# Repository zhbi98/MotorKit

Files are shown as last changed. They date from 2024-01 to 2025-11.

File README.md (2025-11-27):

## ODriveX

一款基于 STM32F405 的高性能开源磁场定向控制（FOC）驱动器，逆变电路采用了英飞凌的 DirectFET-MOS 管，支持高达 100A 持续电流 和 3kW 电机功率，适用于机器人、无人机、CNC 等高动态应用场景。

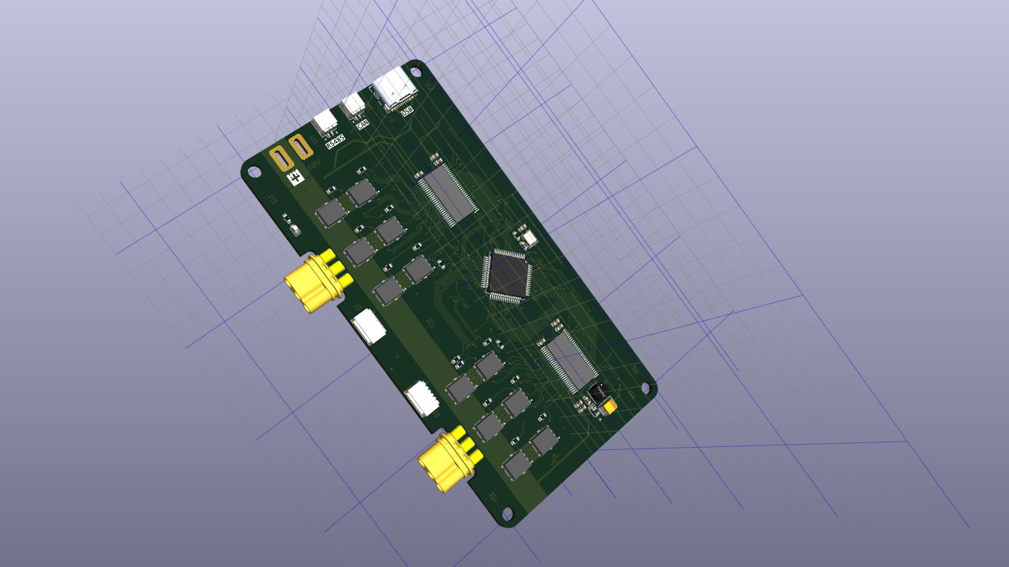
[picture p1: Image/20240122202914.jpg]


## 核心特性

(1) 高性能功率级：英飞凌 DirectFET MOSFET，60V 耐压，单路 100A 峰值电流

(2) 多总线通信：USB-CDC、UART、RS485（Modbus RTU）、CAN 2.0B

(3) 高精度反馈：支持 AS5047P（14-bit SPI）、ABI 编码器、UVW 霍尔

(4) 现代开发栈：CMake + ARM-GCC + VSCode + OpenOCD 图形化调试

(5) 完整 FOC 控制：电流/速度/位置三闭环，支持 SVPWM、死区补偿、弱磁控制

(6) Step/Dir 兼容：可对接传统运动控制器（如 GRBL、Marlin）

## 硬件

硬件涉及两部分，驱动器主体（驱动器硬件命名为 MotorKit）和编码器模块（AS5047P-Driver）。PCB 打样使用制造输出文件（Gerber），打样时把所有 Gerber 文件压缩为 .zip 文件提供给 PCB 制造商（例如嘉立创）即可，PCB 经过我打样验证无误，Gerber 文件在 HardWare/Gerber 目录下，可直接使用。

原理图和 PCB 使用开源 EDA 工具 KiCAD 设计的，如果你有 KiCAD 也知道怎么使用，可以自己去导出 Gerber 文件。

PCB 采用 4层板设计，如果要编辑 PCB 需要下载 KiCAD，还需要看些教程熟悉使用方法，当然这个 EDA 工具本身也非常易学。

购买电子元器件按照 HardWare 目录下的 ibom.html 表格购买。

KiCAD 官方下载链接： https://www.kicad.org/

驱动器主体 KiCAD 工程目录：HardWare/kiacd_project

编码器模块 KiCAD 工程目录：HardWare/AS5047P/HardWare/kiacd_project

制造输出文件（Gerber）目录：HardWare/Gerber

器件 BOM 目录：HardWare/ibom.html

## 固件

程序固件使用 CMake 进行构建的，然后用 ARM-GCC 进行编译的，并且可以搭配 VSCode 和 OpenOCD 进行图形化调试，当然你可以新建一个 STM32F405 的 Keil 工程，把程序组织到 Keil 中编译也可以。

使用 CMake 要求会编写 CMakeLists.txt 文件，不过我这里已经编写好了，在 Firmware 目录下可以看到。

PCB 上预留了 SWD 调试接口，固件固件就可以使用 SWD 下载。

如果没有 VSCode 的嵌入式开发环境，可以看看这篇文章：https://blog.csdn.net/jf_52001760/article/details/126826393

## 电机

我购买的无刷电机是大疆精灵 3 的拆机无刷电机 2312S 可以在淘宝搜索购买，电机到手后还要进行改装，在电机轴上安装供编码器检测的径向磁铁，磁铁尺寸为 6mmx2mm，磁铁安装注意同心度不要过度偏移，磁铁与编码器的间隙大概为 1.0mm。然后再把把 AS5047 编码器模块固定到电机尾部。

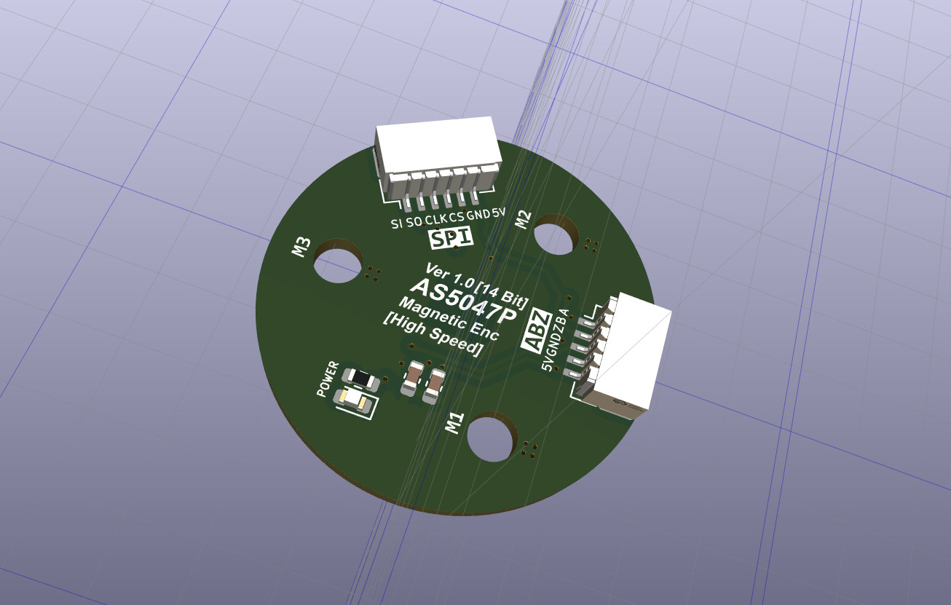
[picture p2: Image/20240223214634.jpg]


## Configuration

控制参数（例如 PID，电流，速度限制等等）都是包含默认值的，所以不需要逐个配置参数电机也能正常工作起来的，必须要注意的是根据实际编码器配置 cpr（例如 AS5047P 编码器使用 ABZ 接口时 CPR 为 1000x4=4000），index 参数，根据电机配置极对数 pole pairs（例如大疆 2312s 电机的极对数为 7），以及按实际调整电流采样电阻，配置一些必须变更的即可。

什么是极对数？

极数是指电机转子（即永磁体部分）磁场中磁极的总数量，磁极总数除以 2 就是极对数，极对数用 P 表示，每个极对包含一个北磁极 N 和一个南磁极 S。

## Start-up

(1) 电机校准（实际就是测量电机的相电阻和相电感）。

(2) 搜索定位编码器 index 信号（在编码器偏移校准之前必须先搜索 index）。

(3) 编码器偏移校准（Offset 校准）。

(4) 使能闭环状态/开环状态。

(5) 设置控制模式（控制模式包含：位置模式，速度模式，电流模式）。和 (4) 结合起来就得到，位置闭环控制模式，速度闭环控制模式，电流闭环控制模式。

(6) 设置控制模式目标值（位置值，速度值，电流值）来调节电机运行状态。

(7) 电机因异常停止后清除错误重新使能进入闭环状态即可。

## Command

CAN 通信协议和 Shell 交互命令实现分别位于 [communication/can/odrive_can.cpp](communication/can/odrive_can.cpp) 和 [ThirdParty/LetterShell/src/shell_cmd_list.c](ThirdParty/LetterShell/src/shell_cmd_list.c) 文件，具体可查看这两个文件，这里列出电机运行起来必要的 Shell 指令，使用 USB 数据线线连接板子 TypeC 和 PC，在 PC 上使用串口调试助手
下发下列指令即可控制。

```cpp
设置最大负电流
odrive:/$ dc_max_negative_current "-2.0"

速度限制 50 turn/s
odrive:/$ controller_config_vel_limit 0 "50.0"

设置电机 0 进入校准状态
odrive:/$ axis_requested_state 0 3

设置电机 0 进入力矩控制模式
odrive:/$ controller_config_control_mode 0 1

设置电机 0 控制力矩
odrive:/$ controller_input_torque 0 "0.02"

进入闭环
odrive:/$ axis_requested_state 0 8

打印当前错误
odrive:/$ dump_errors 1
```

## Step/Dir

Choose any two of the unused GPIOs for step/dir input. Let’s say you chose GPIO7 for the step signal and GPIO8 for the dir signal.

选择任意两个未使用的 GPIO 即可用于 step 和 dir 信号步骤/输入，假设您选择 GPIO7 作为步长信号，GPIO8 选择用于 dir 信号。

这种是基于 step 对应 GPIO 中断对外部电平输入步数累计（中断次数累计），达到位置控制信号可以通过普通 GPIO 输入的目的，

注意这不是 PWM 输入控制模式，两者是有区别的。

This is the simplest possible way of controlling the ODrive. It is also the most primitive and fragile one. So don’t use it unless you must interoperate with other hardware that you don’t control.

这是给驱动器提供控制指令信号最简单的方法。 它也是最原始且最脆弱的一个。因此,除非必须与其他无法控制的硬件进行互操作,否则请勿使用。

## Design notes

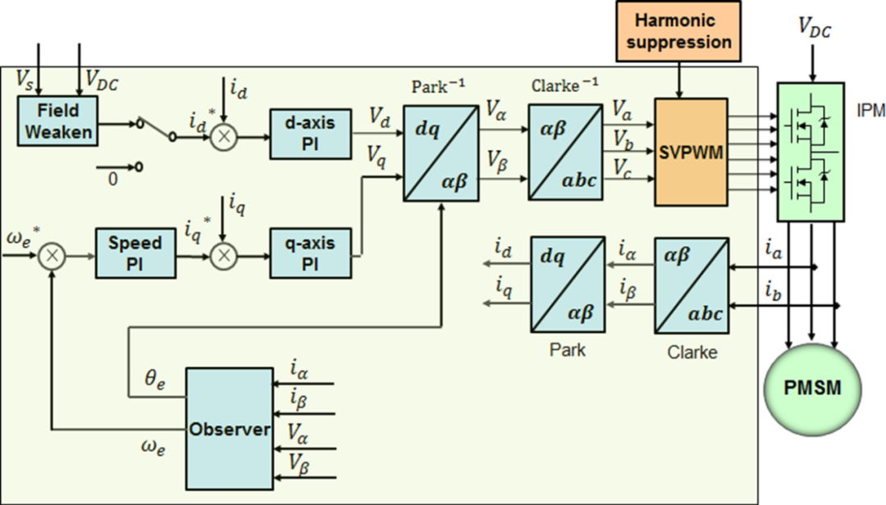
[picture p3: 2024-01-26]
Docs/Control/FOC控制系统框图.png

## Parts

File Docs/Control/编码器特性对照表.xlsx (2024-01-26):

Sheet: Rotary
 | Type | Resolution | Noise (RMS) | max speed | Price | link | Interfaces |  |  | Electrical connection |  | Notes
Note: only encoders with bandwidth (filter cutoff) >200Hz are considered |  | Count/rev | deg | RPM | for 10 units |  | Quadrature | index | absolute | Single ended | Differential
Generic 600ppr encoder | shaft | 2400 | 0.0433 | 4500 | 12 | https://www.aliexpress.com/item/360-600P-R-Photoelectric-Incremental-Rotary-Encoder-5-24V-AB-Two-Phases-Shaft/32756209569.html | y | n | n | y | n
CUI - AMT102 | through bore | 8192 | 0.0127 | 7500 | 24 | https://www.digikey.com/product-detail/en/cui-inc/AMT102-V/102-1307-ND/827015 | y | y | n | y | y
CUI - AMT112 | through bore | 16384 | 0.0063 | 4000 | 32 | https://www.digikey.com/product-detail/en/cui-inc/AMT112S-V/102-3316-ND/4835227 | y | y | n | y | y
USDigital - E6 | through bore | 40000 | 0.0026 | 4320 | 67 | https://www.usdigital.com/products/encoders/incremental/rotary/kit/E6 | y | y | n | y | y
CUI - AMT232B | through bore | 16384 | 0.0063 | 4000 | 49 | https://www.digikey.com/product-detail/en/cui-inc/AMT232B-V/102-4485-ND/8031587 | n | y | y | y | n
CUI - AMT212B | through bore | 16384 | 0.0063 | 4000 | 49 | https://www.digikey.com/product-detail/en/cui-inc/AMT212B-V/102-4527-ND/8537386 | n | y | y | n | y
AMS - AS5047P | on-axis chip | 16384 | 0.0680 | 28000 | 10.61 | https://www.digikey.com/product-detail/en/ams/AS5047P-ATSM/AS5047P-ATSMCT-ND/5287312 | n | y | y | y | n
AMS - AS5047U | on-axis chip | 16384 | 0.0480 | 28000 |  |  | y | y | y | y | n | NPI, not yet stocked?
MagAlpha - MA702 | on-axis chip | 4096 | 0.0300 | 60000 | 5.1 | https://www.digikey.com/product-detail/en/monolithic-power-systems-inc/MA702GQ-Z/1589-1516-1-ND/9433282 | n | y | y | y | n
Infineon - TLE5012 | on-axis chip | 16384 | 0.0500
AMS - AS5311 (w 128p mag ring) | multipole off-axis | 262144 | 0.0017 | 1099.21875 | 15 | https://www.digikey.com/product-detail/en/ams/AS5311-ATST-500/AS5311-ATST-500CT-ND/5892379 | y | n | n | y | n | Has stocking issues
Firmware to read absolute encoders coming soon.
ODrive does not have a receiver for differential encoders, you will have to add that yourself.

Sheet: Linear
 | Type | Resolution | Noise (RMS) | max speed | Price | link | Interfaces |  |  | Electrical connection |  | Notes
Note: only encoders with bandwidth (filter cutoff) >200Hz are considered |  | um | um | m/s | for 10 units |  | Quadrature | index | absolute | Single ended | Differential
AMS - AS5311 | magnetic | 0.49 | 0.60 | 2.35 | 12 | https://www.digikey.com/product-detail/en/ams/AS5311-ATST-500/AS5311-ATST-500CT-ND/5892379 | y | y | y | y | n | Has stocking issues
USDigital - EM2 | transmissive | 3.18 | 0.92 | 9.10 | 35 | https://www.usdigital.com/products/encoders/incremental/modules/EM2 | y | y | n | y | n

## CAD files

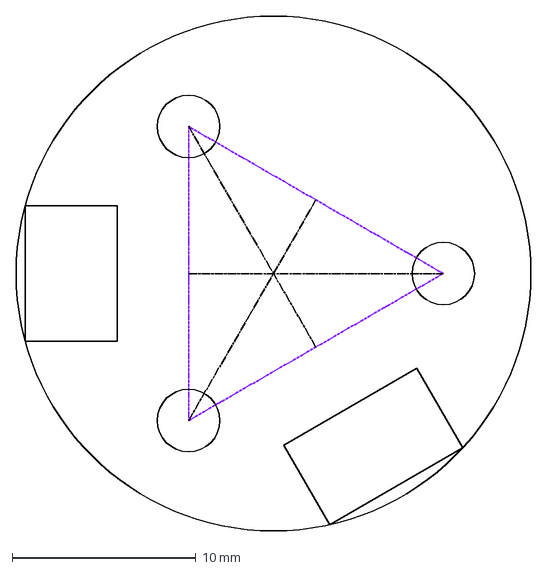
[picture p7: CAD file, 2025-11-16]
HardWare/AS5047P/AS5047P_TOP.dxf
28.0 x 28.0 mm

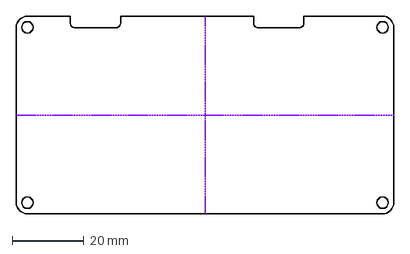
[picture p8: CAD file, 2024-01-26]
HardWare/EDG.dxf
105.0 x 55.0 mm

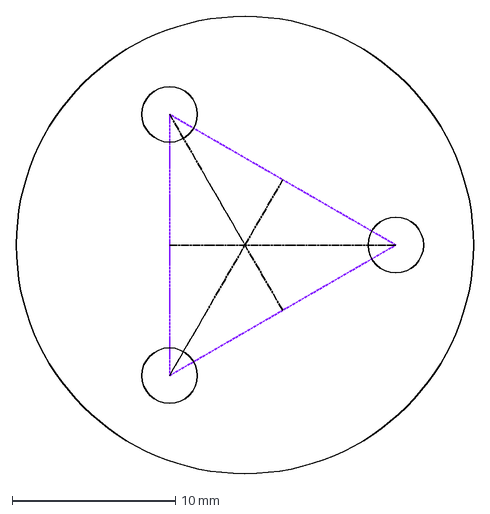
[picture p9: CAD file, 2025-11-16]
HardWare/AS5047P/AS5047P_EDG.dxf
28.0 x 28.0 mm

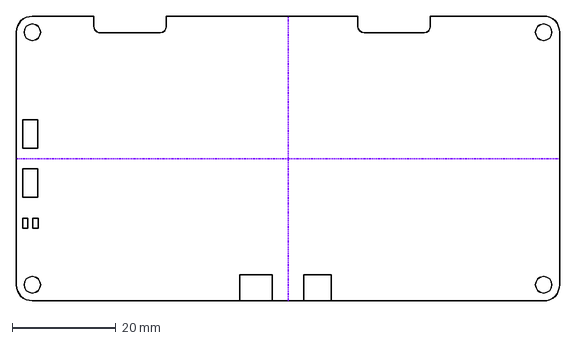
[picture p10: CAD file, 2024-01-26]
HardWare/BOM.dxf
105.0 x 55.0 mm

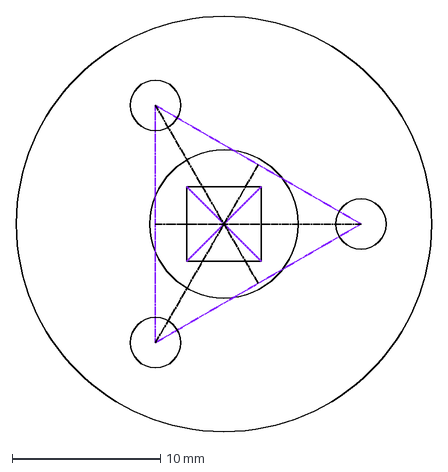
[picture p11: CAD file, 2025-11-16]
HardWare/AS5047P/AS5047P_BOM.dxf
28.0 x 28.0 mm

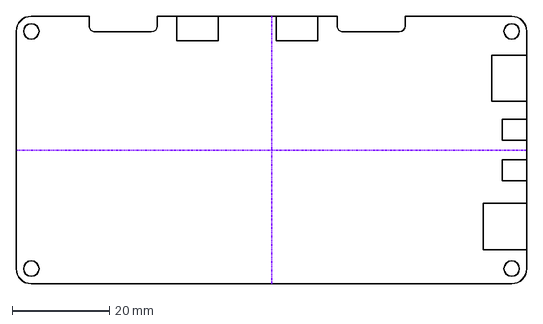
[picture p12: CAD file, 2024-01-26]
HardWare/TOP.dxf
105.0 x 55.0 mm

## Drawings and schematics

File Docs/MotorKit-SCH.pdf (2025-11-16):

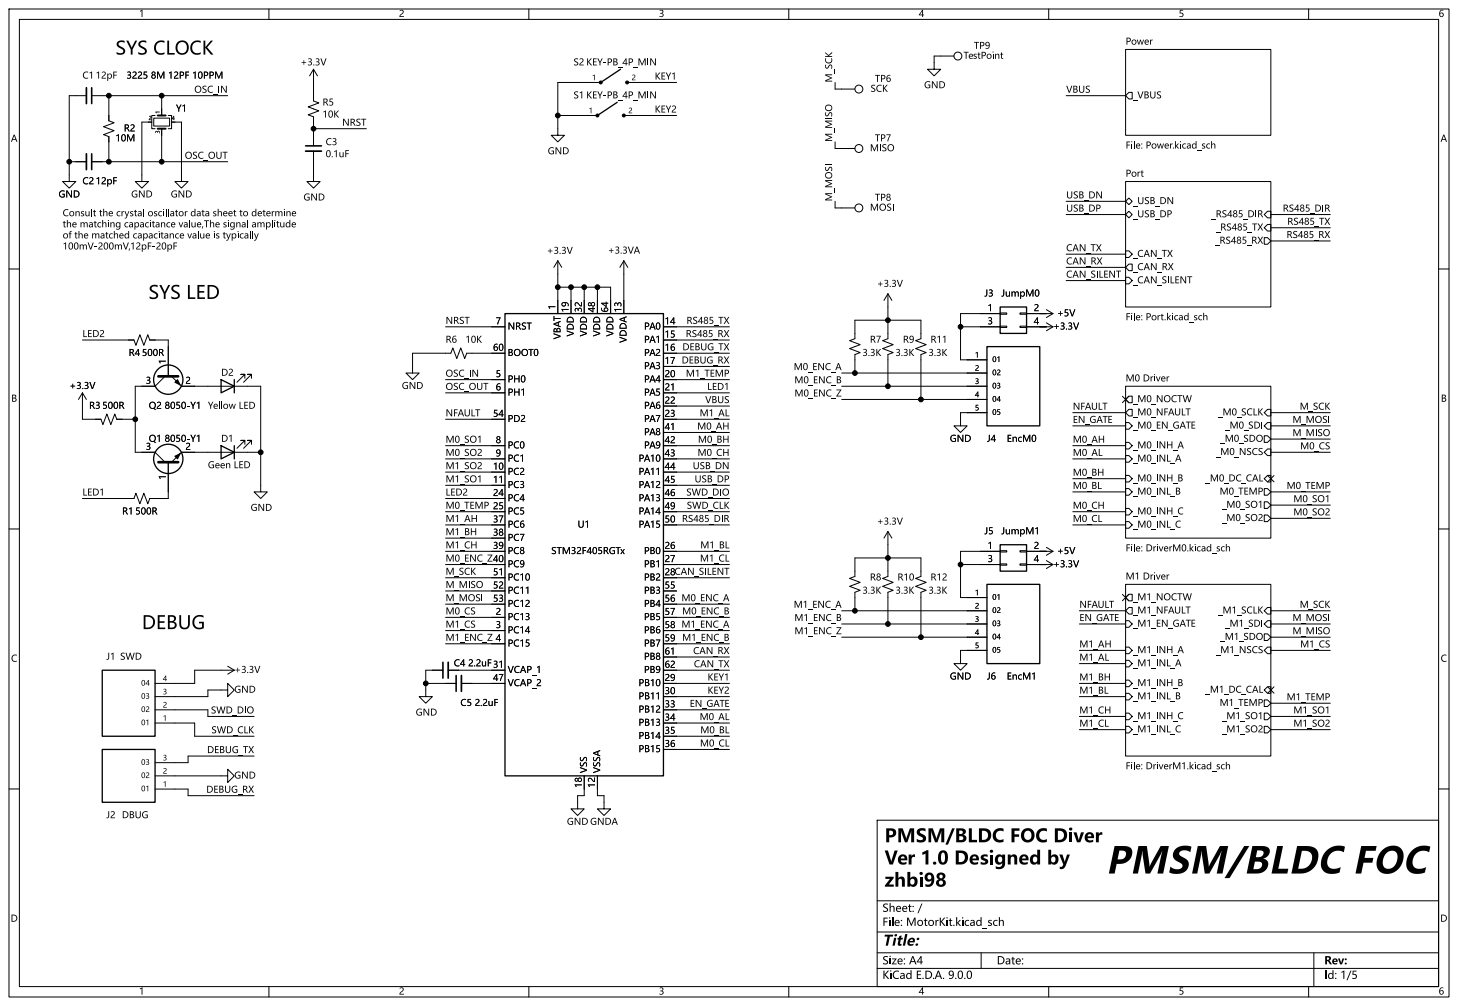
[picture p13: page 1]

GND
of the matched capacitance value is typically

1 VDD 19 VDD 32 VSS 18 VDD 48 VSSA 12 VDD 64 VDDA 13 PA0

Id: 1/5 Title: File: MotorKit.kicad_sch Sheet: /

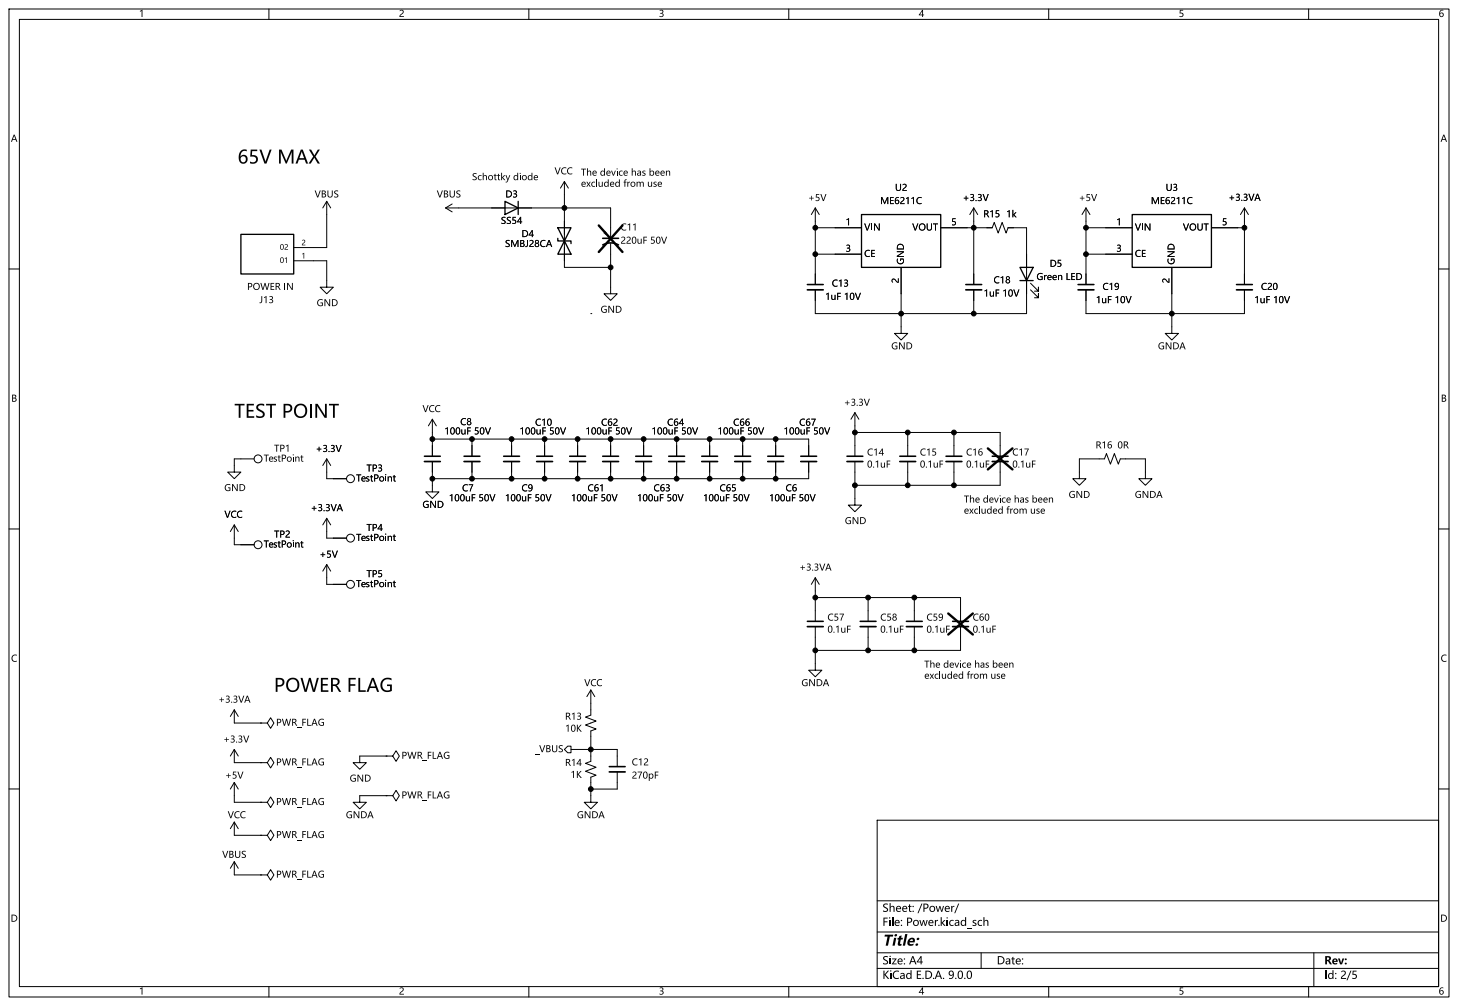
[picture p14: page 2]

The device has been
VCC

excluded from use TESTPOINT

Id: 2/5 Title: File: Power.kicad_sch Sheet: /Power/ C65

excluded from use POWER FLAG

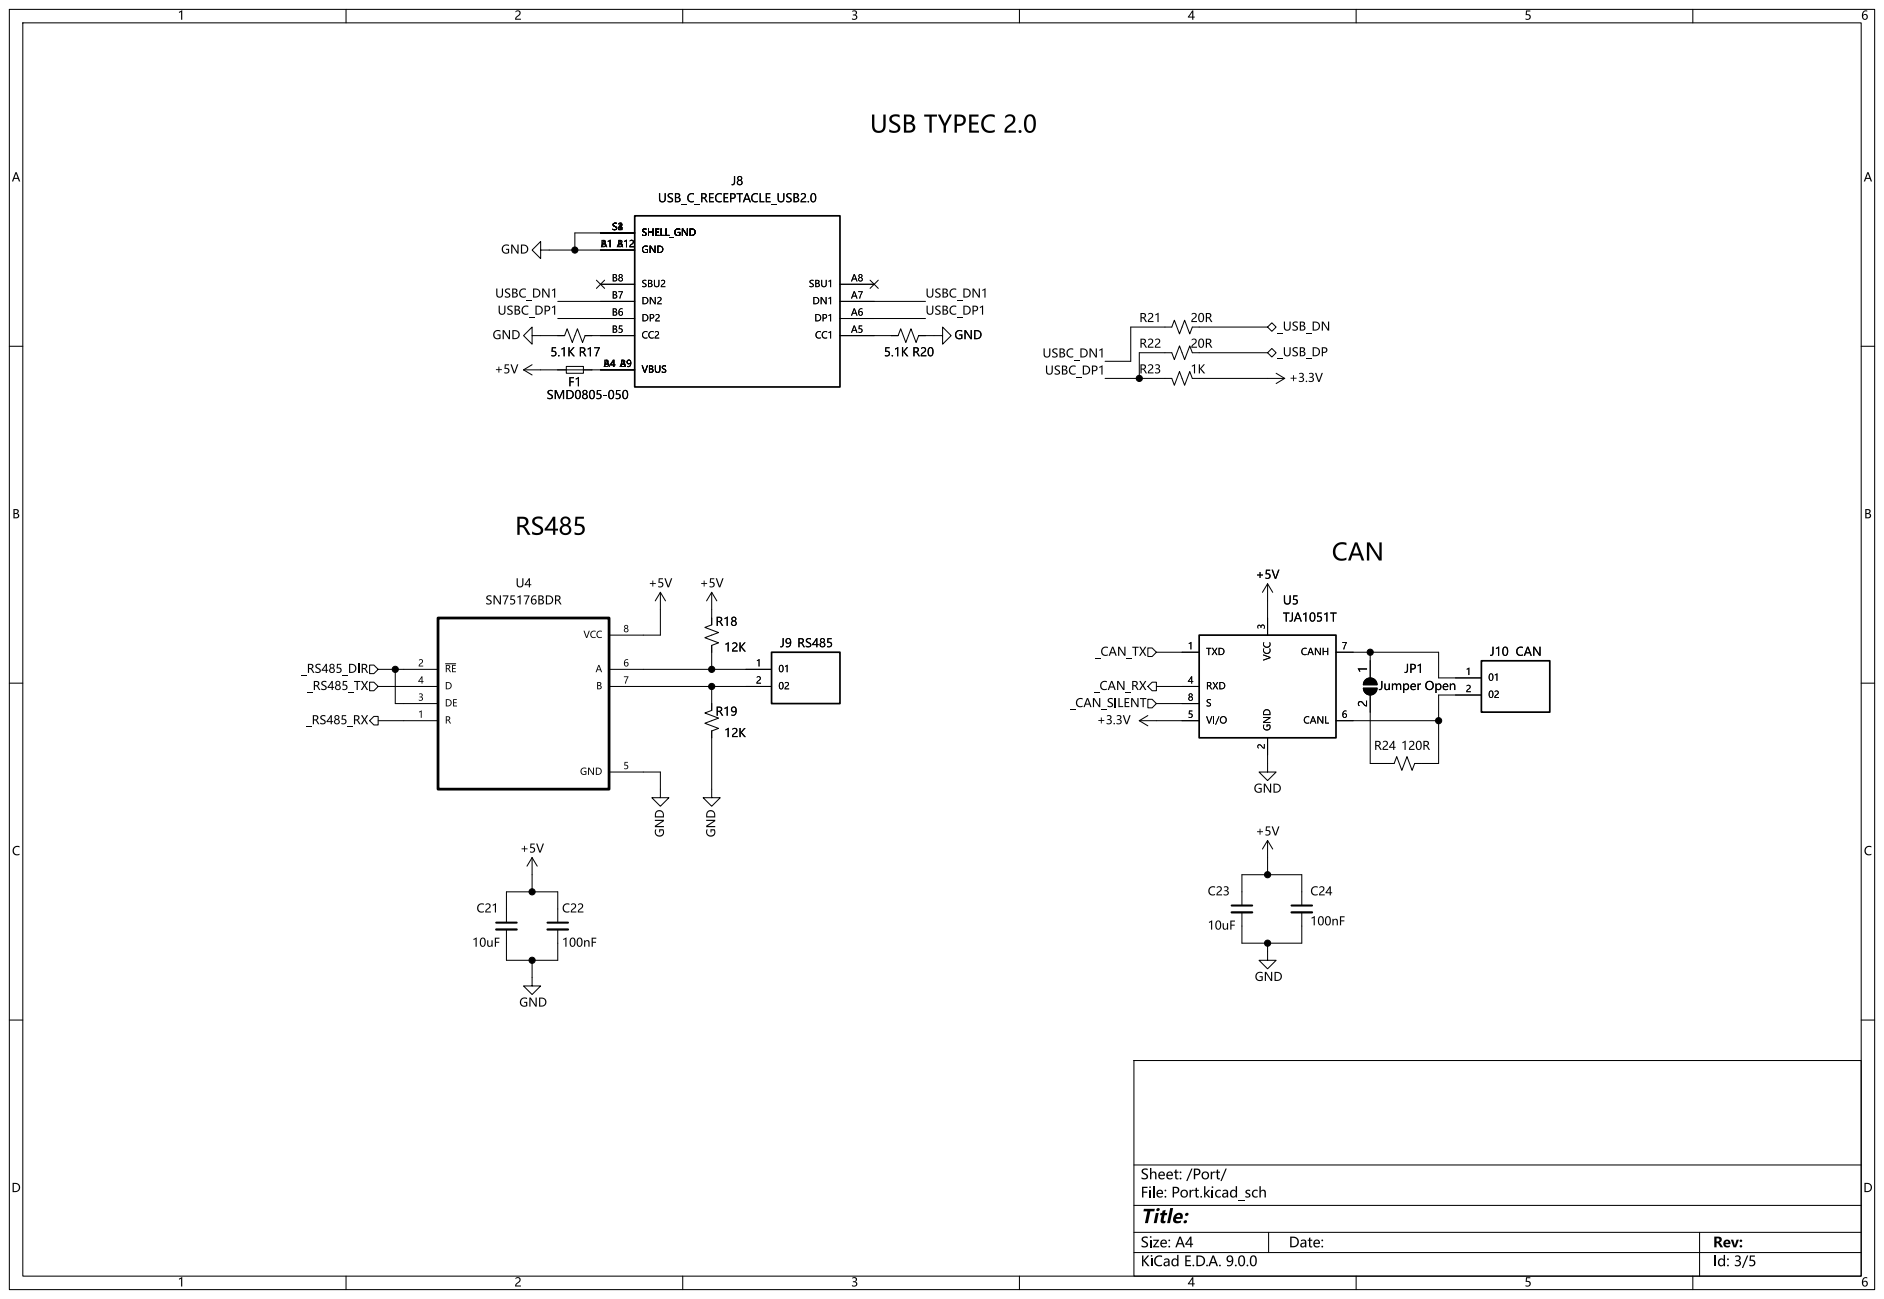
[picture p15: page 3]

Id: 3/5 Title: File: Port.kicad_sch Sheet: /Port/

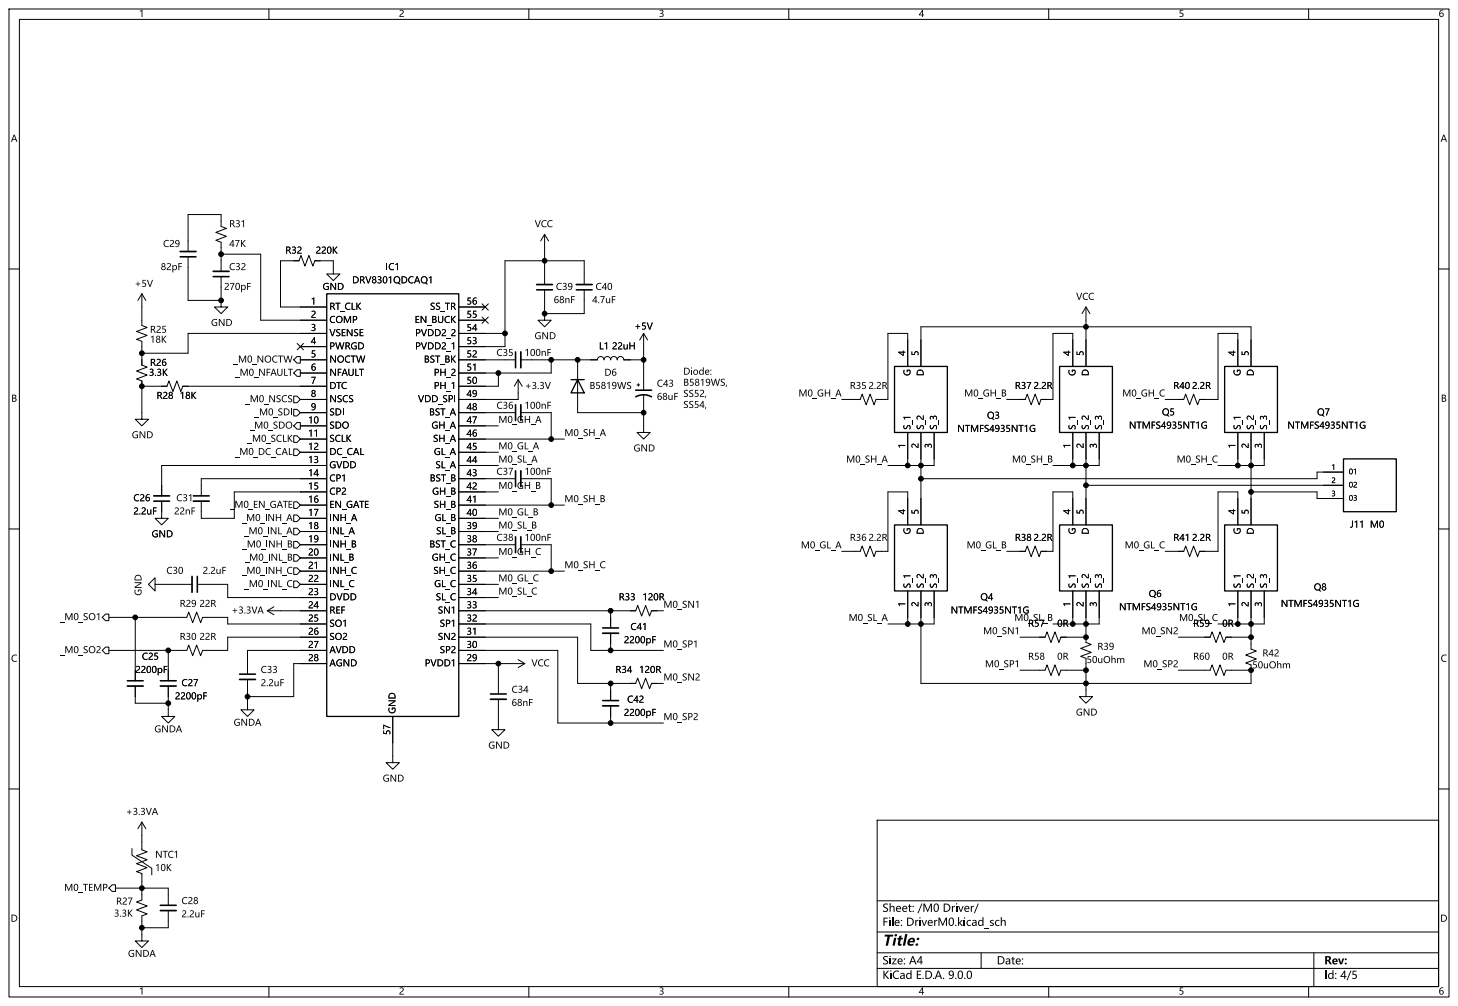
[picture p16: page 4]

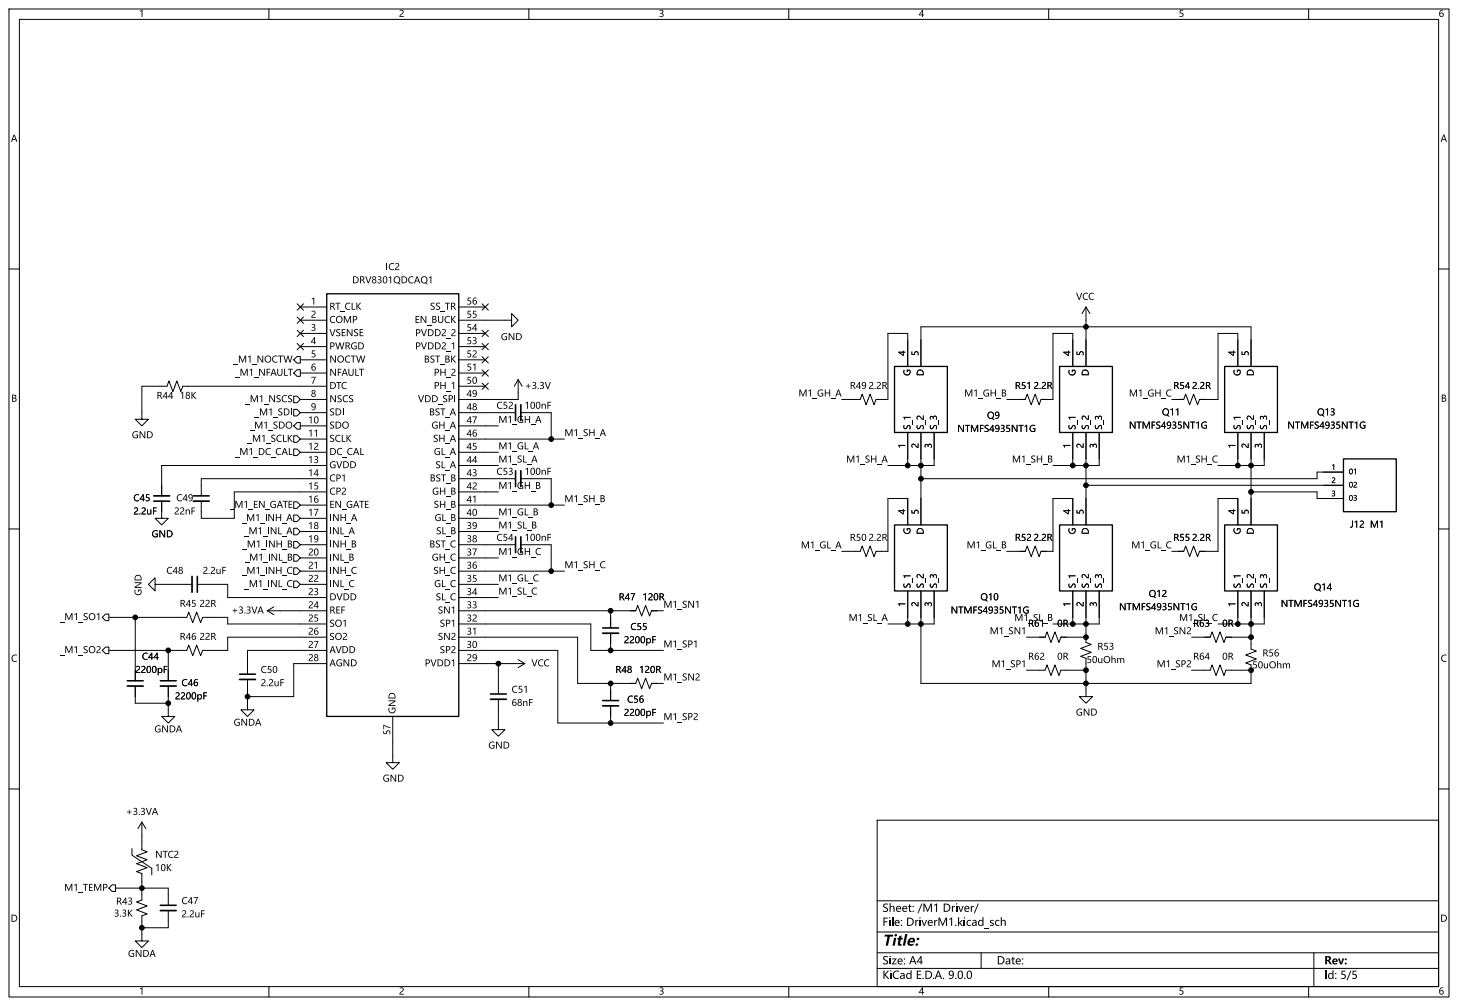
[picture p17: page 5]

Id: 5/5 Title: File: DriverM1.kicad_sch Sheet: /M1 Driver/

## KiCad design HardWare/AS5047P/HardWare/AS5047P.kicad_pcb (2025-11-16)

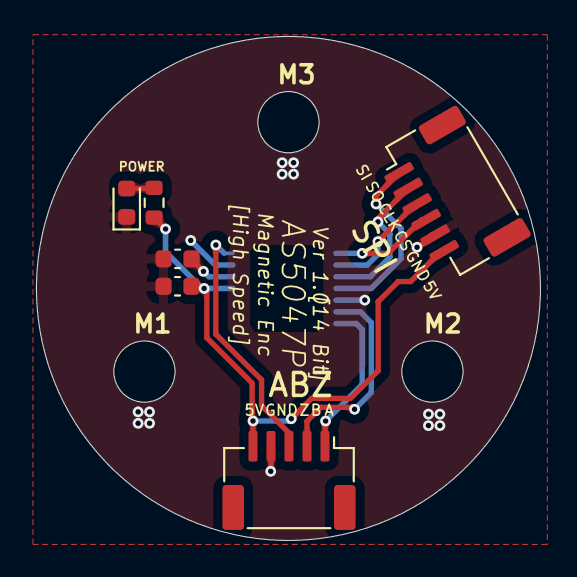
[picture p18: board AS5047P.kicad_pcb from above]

Board: 2 copper layers, 28.0 x 28.0 mm, 7 parts (1 on the bottom side), 11 nets.

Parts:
C1: 0.1uF; C_0603_1608Metric
C2: 1uF; C_0603_1608Metric
D1: Yellow LED; LED_0603_1608Metric
J1: CONN_1x5P; CONN-SMD_1x5P-P1.0-H_WAFER-SH1.0-5PWB
J2: CONN_1x5P; CONN-SMD_1x6P-P1.0-H_WAFER-SH1.0-6PWB
R1: 1K; R_0603_1608Metric
U1: AS5047D; TSSOP-14_4.4x5mm_P0.65mm

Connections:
+5V: C1.2, J1.5, J2.6, R1.1, U1.11 (VDD)
/A: J1.1, U1.7 (A)
/B: J1.2, U1.6 (B)
/CLK: J2.3, U1.2 (CLK)
/CS: J2.4, U1.1 (~CS)
/MISO: J2.2, U1.3 (MISO)
/MOSI: J2.1, U1.4 (MOSI)
/Z: J1.3, U1.14 (I/PWM)
GND: C1.1, C2.2, D1.1 (K), J1.4, J2.5, U1.5 (TST), U1.13 (GND)
unnamed: D1.2 (A), R1.2
unnamed: C2.1, U1.12 (VDD3V3)

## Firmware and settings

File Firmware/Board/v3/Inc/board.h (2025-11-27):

/*
* @brief Contains board specific configuration for ODrive v3.x
*/

#ifndef __BOARD_CONFIG_H
#define __BOARD_CONFIG_H

#include <stdbool.h>

// STM specific includes
#include <stm32f4xx_hal.h>
#include <gpio.h>
#include <spi.h>
#include <tim.h>
#include <can.h>
#include <i2c.h>
#include <usb_device.h>
#include <main.h>
#include "cmsis_os.h"

#include <arm_math.h>

#include <Drivers/STM32/stm32_system.h>

/*------ Add by zhbi98 -------*/
#define HW_VERSION_VOLTAGE 56U
#define HW_VERSION_MAJOR 3U
#define HW_VERSION_MINOR 6U
/*----------------------------*/

/*------ Modify by zhbi98 ----*/
/*相电流采样电阻设置，该定义要与实际电阻相同或接近，但相差不要超过 10 倍，例如实际为 5mΩ 可以设置为 2mΩ，
但不能设置为 0.5mΩ，否则可能会导致采集不到正确的电流从而产生 ERROR_PHASE_RESISTANCE_OUT_OF_RANGE 和 
ERROR_PHASE_INDUCTANCE_OUT_OF_RANGE 错误。*/
#define SHUNT_RESISTANCE (200e-5f/*500e-6f*/)
/*----------------------------*/

#define AXIS_COUNT (2)
#define CAN_CLK_MHZ (42UL)
#define CAN_CLK_HZ (42000000UL)
#define CAN_FREQ (2000000UL) /*42M/(16tq+4tq+1)*/

#define DEFAULT_BRAKE_RESISTANCE (2.0f) // [ohm]
#define DEFAULT_MIN_DC_VOLTAGE 8.0f

#define TIM_TIME_BASE TIM14

// Run control loop at the same frequency as the current measurements.
#define CONTROL_TIMER_PERIOD_TICKS  (2 * TIM_1_8_PERIOD_CLOCKS * (TIM_1_8_RCR + 1))

#define TIM1_INIT_COUNT (TIM_1_8_PERIOD_CLOCKS / 2 - 1 * 128) // TODO: explain why this offset

// The delta from the control loop timestamp to the current sense timestamp is
// exactly 0 for M0 and TIM1_INIT_COUNT for M1.
#define MAX_CONTROL_LOOP_UPDATE_TO_CURRENT_UPDATE_DELTA (TIM_1_8_PERIOD_CLOCKS / 2 + 1 * 128)

#ifdef __cplusplus
#include <Drivers/DRV8301/drv8301.hpp>
#include <Drivers/STM32/stm32_gpio.hpp>
#include <Drivers/STM32/stm32_spi_arbiter.hpp>
#include <MotorControl/pwm_input.hpp>
#include <MotorControl/thermistor.hpp>

using TGateDriver = Drv8301;
using TOpAmp = Drv8301;

#include <MotorControl/motor.hpp>
#include <MotorControl/encoder.hpp>

extern std::array<Axis, AXIS_COUNT> axes;
extern Motor motors[AXIS_COUNT];
extern OnboardThermistorCurrentLimiter fet_thermistors[AXIS_COUNT];
extern Encoder encoders[AXIS_COUNT];

extern USBD_HandleTypeDef& usb_dev_handle;

extern PwmInput pwm0_input;
#endif

// Period in [s]
#define CURRENT_MEAS_PERIOD ( (float)2*TIM_1_8_PERIOD_CLOCKS*(TIM_1_8_RCR+1) / (float)TIM_1_8_CLOCK_HZ )
static const float current_meas_period = CURRENT_MEAS_PERIOD;

// Frequency in [Hz]
#define CURRENT_MEAS_HZ ( (float)(TIM_1_8_CLOCK_HZ) / (float)(2*TIM_1_8_PERIOD_CLOCKS*(TIM_1_8_RCR+1)) )
static const int current_meas_hz = CURRENT_MEAS_HZ;

#if HW_VERSION_VOLTAGE >= 48
#define VBUS_S_DIVIDER_RATIO 19.0f
#elif HW_VERSION_VOLTAGE == 24
#define VBUS_S_DIVIDER_RATIO 11.0f
#else
#error "unknown board voltage"
#endif

// Linear range of the DRV8301 opamp output: 0.3V...5.7V. We set the upper limit
// to 3.0V so that it's symmetric around the center point of 1.65V.
#define CURRENT_SENSE_MIN_VOLT  0.3f
#define CURRENT_SENSE_MAX_VOLT  3.0f

// This board has no board-specific user configurations
static inline bool board_read_config() { return true; }
static inline bool board_write_config() { return true; }
static inline void board_clear_config() { }
static inline bool board_apply_config() { return true; }

void system_init();
bool board_init();
void start_timers();

#endif // __BOARD_CONFIG_H

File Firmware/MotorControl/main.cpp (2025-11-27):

#define __MAIN_CPP__
#include "odrive_main.h"
#include "nvm_config.hpp"

#include "usart.h"
#include "freertos_vars.h"
#include "usb_device.h"

osSemaphoreId sem_usb_irq;
osMessageQId uart_event_queue;
osMessageQId usb_event_queue;
osSemaphoreId sem_can;

#if defined(STM32F405xx)
// Place FreeRTOS heap in core coupled memory for better performance
__attribute__((section(".ccmram")))
#endif
uint8_t ucHeap[configTOTAL_HEAP_SIZE];
// FreeRTOS 允许应用程序开发者在外部定义堆的数组，同时利用 ".ccmram" 指令，将
// FreeRTOS 的堆数组放在 STM32 的 ccm 内存（CCM-RAM）中可以获得更好的性能。

uint32_t _reboot_cookie __attribute__ ((section (".noinit")));
extern char _estack; // provided by the linker script


ODrive odrv{};


ConfigManager config_manager;

static bool config_read_all() {
    /**从 NVM (芯片 Flash) 中加载 (读取) '板载配置参数' config_ 字段，
    编码器偏移校准参数到指定的各个结构体对象指针（内存）中。*/
    bool success = board_read_config() &&
           config_manager.read(&odrv.config_) &&
           config_manager.read(&odrv.can_.config_);

    /**从 NVM (芯片 Flash) 中加载 (读取) '电机配置参数'，config_ 字段，
    编码器偏移校准参数到指定的各个结构体对象指针（内存）中。*/
    for (size_t i = 0; (i < AXIS_COUNT) && success; ++i) {
        success = config_manager.read(&encoders[i].config_) &&
                  config_manager.read(&axes[i].sensorless_estimator_.config_) &&
                  config_manager.read(&axes[i].controller_.config_) &&
                  config_manager.read(&axes[i].trap_traj_.config_) &&
                  config_manager.read(&axes[i].min_endstop_.config_) &&
                  config_manager.read(&axes[i].max_endstop_.config_) &&
                  config_manager.read(&axes[i].mechanical_brake_.config_) &&
                  config_manager.read(&motors[i].config_) &&
                  config_manager.read(&motors[i].fet_thermistor_.config_) &&
                  config_manager.read(&motors[i].motor_thermistor_.config_) &&
                  config_manager.read(&axes[i].config_);
    }
    return success;
}

static bool config_write_all() {
    /**板载配置参数没有集中定义，而是分布定义到各个对象的 config_ 字段，
     * 各个对象的config_ 字段写入 NVM (芯片 Flash) 中。*/
    bool success = board_write_config() &&
           config_manager.write(&odrv.config_) &&
           config_manager.write(&odrv.can_.config_);
    for (size_t i = 0; (i < AXIS_COUNT) && success; ++i) {
        success = config_manager.write(&encoders[i].config_) &&
                  config_manager.write(&axes[i].sensorless_estimator_.config_) &&
                  config_manager.write(&axes[i].controller_.config_) &&
                  config_manager.write(&axes[i].trap_traj_.config_) &&
                  config_manager.write(&axes[i].min_endstop_.config_) &&
                  config_manager.write(&axes[i].max_endstop_.config_) &&
                  config_manager.write(&axes[i].mechanical_brake_.config_) &&
                  config_manager.write(&motors[i].config_) &&
                  config_manager.write(&motors[i].fet_thermistor_.config_) &&
                  config_manager.write(&motors[i].motor_thermistor_.config_) &&
                  config_manager.write(&axes[i].config_);
    }
    return success;
}

static void config_clear_all() {
    /**清除 NVM (芯片 Flash) 中的各类配置参数并给各个结构体对象赋予默认值*/
    odrv.config_ = {};
    odrv.can_.config_ = {};
    for (size_t i = 0; i < AXIS_COUNT; ++i) {
        encoders[i].config_ = {};
        axes[i].sensorless_estimator_.config_ = {};
        axes[i].controller_.config_ = {};
        axes[i].controller_.config_.load_encoder_axis = i;
        axes[i].trap_traj_.config_ = {};
        axes[i].min_endstop_.config_ = {};
        axes[i].max_endstop_.config_ = {};
        axes[i].mechanical_brake_.config_ = {};
        motors[i].config_ = {};
        motors[i].fet_thermistor_.config_ = {};
        motors[i].motor_thermistor_.config_ = {};
        axes[i].clear_config();
    }
}

static bool config_apply_all() {
    bool success = odrv.can_.apply_config();
    for (size_t i = 0; (i < AXIS_COUNT) && success; ++i) {
        success = encoders[i].apply_config(motors[i].config_.motor_type)
               && axes[i].controller_.apply_config()
               && axes[i].min_endstop_.apply_config()
               && axes[i].max_endstop_.apply_config()
               && motors[i].apply_config()
               && motors[i].motor_thermistor_.apply_config()
               && axes[i].apply_config();
    }
    return success;
}

bool ODrive::save_configuration(void) {
    bool success;

    CRITICAL_SECTION() {
        bool any_armed = std::any_of(axes.begin(), axes.end(),
            [](auto& axis){ return axis.motor_.is_armed_; });
        if (any_armed) {
            return false;
        }

        size_t config_size = 0;
        success = config_manager.prepare_store()
               && config_write_all()
               && config_manager.start_store(&config_size)
               && config_write_all()
               && config_manager.finish_store();

        // FIXME: during save_configuration we might miss some interrupts
        // because the CPU gets halted during a flash erase. Missing events
        // (encoder updates, step/dir steps) is not good so to be sure we just
        // reboot.
        NVIC_SystemReset();
    }

    return success;
}

void ODrive::erase_configuration(void) {
    NVM_erase();

    // FIXME: this reboot is a workaround because we don't want the next save_configuration
    // to write back the old configuration from RAM to NVM. The proper action would
    // be to reset the values in RAM to default. However right now that's not
    // practical because several startup actions depend on the config. The
    // other problem is that the stack overflows if we reset to default here.
    NVIC_SystemReset();
}

void ODrive::enter_dfu_mode() {
    if ((hw_version_major_ == 3) && (hw_version_minor_ >= 5)) {
        __asm volatile ("CPSID I\n\t":::"memory"); // disable interrupts
        _reboot_cookie = 0xDEADBEEF;
        NVIC_SystemReset();
    } else {
        /*
        * DFU mode is only allowed on board version >= 3.5 because it can burn
        * the brake resistor FETs on older boards.
        * If you really want to use it on an older board, add 3.3k pull-down resistors
        * to the AUX_L and AUX_H signals and _only then_ uncomment these lines.
        */
        //__asm volatile ("CPSID I\n\t":::"memory"); // disable interrupts
        //_reboot_cookie = 0xDEADFE75;
        //NVIC_SystemReset();
    }
}

bool ODrive::any_error() {
    return error_ != ODrive::ERROR_NONE
        || std::any_of(axes.begin(), axes.end(), [](Axis& axis){
            return axis.error_ != Axis::ERROR_NONE
                || axis.motor_.error_ != Motor::ERROR_NONE
                || axis.sensorless_estimator_.error_ != SensorlessEstimator::ERROR_NONE
                || axis.encoder_.error_ != Encoder::ERROR_NONE
                || axis.controller_.error_ != Controller::ERROR_NONE;
        });
}

uint64_t ODrive::get_drv_fault() {
#if AXIS_COUNT == 1
    return motors[0].gate_driver_.get_error();
#elif AXIS_COUNT == 2
    return (uint64_t)motors[0].gate_driver_.get_error() | ((uint64_t)motors[1].gate_driver_.get_error() << 32ULL);
#else
    #error "not supported"
#endif
}

/**清除电机所有错误，清除错误后电机才能继续接收运行指令*/
void ODrive::clear_errors() {
    for (auto& axis: axes) {
        axis.motor_.error_ = Motor::ERROR_NONE;
        axis.controller_.error_ = Controller::ERROR_NONE;
        axis.sensorless_estimator_.error_ = SensorlessEstimator::ERROR_NONE;
        axis.encoder_.error_ = Encoder::ERROR_NONE;
        axis.encoder_.spi_error_rate_ = 0.0f;
        axis.error_ = Axis::ERROR_NONE;
    }
    error_ = ERROR_NONE;
    if (odrv.config_.enable_brake_resistor) {
        safety_critical_arm_brake_resistor();
    }
}

extern "C" {

void vApplicationStackOverflowHook(xTaskHandle *pxTask, signed portCHAR *pcTaskName) {
    for(auto& axis: axes){
        axis.motor_.disarm();
    }
    safety_critical_disarm_brake_resistor();
    for (;;); // TODO: safe action
}

void vApplicationIdleHook(void) {
    if (odrv.system_stats_.fully_booted) {
        odrv.system_stats_.uptime = xTaskGetTickCount();
        odrv.system_stats_.min_heap_space = xPortGetMinimumEverFreeHeapSize();

        uint32_t min_stack_space[AXIS_COUNT];
        std::transform(axes.begin(), axes.end(), std::begin(min_stack_space), [](auto& axis) { return uxTaskGetStackHighWaterMark(axis.thread_id_) * sizeof(StackType_t); });
        odrv.system_stats_.max_stack_usage_axis = axes[0].stack_size_ - *std::min_element(std::begin(min_stack_space), std::end(min_stack_space));
        /*odrv.system_stats_.max_stack_usage_usb = stack_size_usb_thread - uxTaskGetStackHighWaterMark(usb_thread) * sizeof(StackType_t); Modify by zhbi98*/
        /*odrv.system_stats_.max_stack_usage_uart = stack_size_uart_thread - uxTaskGetStackHighWaterMark(uart_thread) * sizeof(StackType_t); Modify by zhbi98*/
        odrv.system_stats_.max_stack_usage_startup = stack_size_default_task - uxTaskGetStackHighWaterMark(defaultTaskHandle) * sizeof(StackType_t);
        /*odrv.system_stats_.max_stack_usage_can = odrv.can_.stack_size_ - uxTaskGetStackHighWaterMark(odrv.can_.thread_id_) * sizeof(StackType_t);*/
        odrv.system_stats_.max_stack_usage_analog =  stack_size_analog_thread - uxTaskGetStackHighWaterMark(analog_thread) * sizeof(StackType_t);

        odrv.system_stats_.stack_size_axis = axes[0].stack_size_;
        /*odrv.system_stats_.stack_size_usb = stack_size_usb_thread; Modify by zhbi98*/
        /*odrv.system_stats_.stack_size_uart = stack_size_uart_thread; Modify by zhbi98*/
        odrv.system_stats_.stack_size_startup = stack_size_default_task;
        odrv.system_stats_.stack_size_can = odrv.can_.stack_size_;
        odrv.system_stats_.stack_size_analog = stack_size_analog_thread;

        odrv.system_stats_.prio_axis = osThreadGetPriority(axes[0].thread_id_);
        /*odrv.system_stats_.prio_usb = osThreadGetPriority(usb_thread); Modify by zhbi98*/
        /*odrv.system_stats_.prio_uart = osThreadGetPriority(uart_thread); Modify by zhbi98*/
        odrv.system_stats_.prio_startup = osThreadGetPriority(defaultTaskHandle);
        /*odrv.system_stats_.prio_can = osThreadGetPriority(odrv.can_.thread_id_);*/
        odrv.system_stats_.prio_analog = osThreadGetPriority(analog_thread);
    }
}
}

/**
 * @brief Runs system-level checks that need to be as real-time as possible.
 * 
 * This function is called after every current measurement of every motor.
 * It should finish as quickly as possible.
 */
void ODrive::do_fast_checks() {
    if (!(vbus_voltage >= config_.dc_bus_undervoltage_trip_level))
        disarm_with_error(ERROR_DC_BUS_UNDER_VOLTAGE);
    if (!(vbus_voltage <= config_.dc_bus_overvoltage_trip_level))
        disarm_with_error(ERROR_DC_BUS_OVER_VOLTAGE);
}

/**
 * @brief Floats all power phases on the system (all motors and brake resistors).
 *
 * This should be called if a system level exception ocurred that makes it
 * unsafe to run power through the system in general.
 */
void ODrive::disarm_with_error(Error error) {
    CRITICAL_SECTION() {
        for (auto& axis: axes) {
            /*发生系统级错误，例如：总线电压过低，总线电压过高*/
            axis.motor_.disarm_with_error(Motor::ERROR_SYSTEM_LEVEL);
        }
        safety_critical_disarm_brake_resistor();
        error_ |= error;
    }
}

/**
 * @brief Runs the periodic sampling tasks
 * 
 * All components that need to sample real-world data should do it in this
 * function as it runs on a high interrupt priority and provides lowest possible
 * timing jitter.
 * 
 * All function called from this function should adhere to the following rules:
 *  - Try to use the same number of CPU cycles in every iteration.
 *    (reason: Tasks that run later in the function still want lowest possible timing jitter)
 *  - Use as few cycles as possible.
 *    (reason: The interrupt blocks other important interrupts (TODO: which ones?))
 *  - Not call any FreeRTOS functions.
 *    (reason: The interrupt priority is higher than the max allowed priority for syscalls)
 * 
 * Time consuming and undeterministic logic/arithmetic should live on
 * control_loop_cb() instead.
 */
void ODrive::sampling_cb() {
    n_evt_sampling_++;

    MEASURE_TIME(task_times_.sampling) {
        for (auto& axis: axes) {
            axis.encoder_.sample_now();
        }
    }
}

/**
 * @brief Runs the periodic control loop.
 * 
 * This function is executed in a low priority interrupt context and is allowed
 * to call CMSIS functions.
 * 
 * Yet it runs at a higher priority than communication workloads.
 * 
 * @param update_cnt: The true count of update events (wrapping around at 16
 *        bits). This is used for timestamp calculation in the face of
 *        potentially missed timer update interrupts. Therefore this counter
 *        must not rely on any interrupts.
 */
void ODrive::control_loop_cb(uint32_t timestamp) {
    last_update_timestamp_ = timestamp;
    n_evt_control_loop_++;

    // TODO: use a configurable component list for most of the following things

    MEASURE_TIME(task_times_.control_loop_misc) {
        // Reset all output ports so that we are certain about the freshness of
        // all values that we use.
        // If we forget to reset a value here the worst that can happen is that
        // this safety check doesn't work.
        // TODO: maybe we should add a check to output ports that prevents
        // double-setting the value.
        for (auto& axis: axes) {
            axis.acim_estimator_.slip_vel_.reset();
            axis.acim_estimator_.stator_phase_vel_.reset();
            axis.acim_estimator_.stator_phase_.reset();
            axis.controller_.torque_output_.reset();
            axis.encoder_.phase_.reset();
            axis.encoder_.phase_vel_.reset();
            axis.encoder_.pos_estimate_.reset();
            axis.encoder_.vel_estimate_.reset();
            axis.encoder_.pos_circular_.reset();
            axis.motor_.Vdq_setpoint_.reset();
            axis.motor_.Idq_setpoint_.reset();
            axis.open_loop_controller_.Idq_setpoint_.reset();
            axis.open_loop_controller_.Vdq_setpoint_.reset();
            axis.open_loop_controller_.phase_.reset();
            axis.open_loop_controller_.phase_vel_.reset();
            axis.open_loop_controller_.total_distance_.reset();
            axis.sensorless_estimator_.phase_.reset();
            axis.sensorless_estimator_.phase_vel_.reset();
            axis.sensorless_estimator_.vel_estimate_.reset();
        }

        /*uart_poll();*/
        odrv.oscilloscope_.update();
    }

    for (auto& axis : axes) {
        MEASURE_TIME(axis.task_times_.endstop_update) {
            axis.min_endstop_.update();
            axis.max_endstop_.update();
        }
    }

    MEASURE_TIME(task_times_.control_loop_checks) {
        for (auto& axis: axes) {
            // look for errors at axis level and also all subcomponents
            bool checks_ok = axis.do_checks(timestamp);

            // make sure the watchdog is being fed. 
            bool watchdog_ok = axis.watchdog_check();

            if (!checks_ok || !watchdog_ok) {
                axis.motor_.disarm();
            }
        }
    }

    for (auto& axis: axes) {
        // Sub-components should use set_error which will propegate to this error_
        MEASURE_TIME(axis.task_times_.thermistor_update) {
            axis.motor_.fet_thermistor_.update();
            axis.motor_.motor_thermistor_.update();
        }

        MEASURE_TIME(axis.task_times_.encoder_update)
            axis.encoder_.update();
    }

    // Controller of either axis might use the encoder estimate of the other
    // axis so we process both encoders before we continue.

    for (auto& axis: axes) {
        MEASURE_TIME(axis.task_times_.sensorless_estimator_update)
            axis.sensorless_estimator_.update();

        MEASURE_TIME(axis.task_times_.controller_update) {
            if (!axis.controller_.update()) { // uses position and velocity from encoder
                axis.error_ |= Axis::ERROR_CONTROLLER_FAILED;
            }
        }

        MEASURE_TIME(axis.task_times_.open_loop_controller_update)
            axis.open_loop_controller_.update(timestamp);

        MEASURE_TIME(axis.task_times_.motor_update)
            axis.motor_.update(timestamp); // uses torque from controller and phase_vel from encoder

        MEASURE_TIME(axis.task_times_.current_controller_update)
            axis.motor_.current_control_.update(timestamp); // uses the output of controller_ or open_loop_contoller_ and encoder_ or sensorless_estimator_ or acim_estimator_
    }

    // Tell the axis threads that the control loop has finished
    for (auto& axis: axes) {
        if (axis.thread_id_) {
            osSignalSet(axis.thread_id_, 0x0001);
        }
    }
}


/** @brief For diagnostics only */
uint32_t ODrive::get_interrupt_status(int32_t irqn) {
    if ((irqn < -14) || (irqn >= 240)) {
        return 0xffffffff;
    }

    uint8_t priority = (irqn < -12)
        ? 0 // hard fault and NMI always have maximum priority
        : NVIC_GetPriority((IRQn_Type)irqn);
    uint32_t counter = GET_IRQ_COUNTER((IRQn_Type)irqn);
    bool is_enabled = (irqn < 0)
        ? true // processor interrupt vectors are always enabled
        : NVIC->ISER[(((uint32_t)(int32_t)irqn) >> 5UL)] & (uint32_t)(1UL << (((uint32_t)(int32_t)irqn) & 0x1FUL));
    
    return priority | ((counter & 0x7ffffff) << 8) | (is_enabled ? 0x80000000 : 0);
}

/** @brief For diagnostics only */
uint32_t ODrive::get_dma_status(uint8_t stream_num) {
    DMA_Stream_TypeDef* streams[] = {
        DMA1_Stream0, DMA1_Stream1, DMA1_Stream2, DMA1_Stream3, DMA1_Stream4, DMA1_Stream5, DMA1_Stream6, DMA1_Stream7,
        DMA2_Stream0, DMA2_Stream1, DMA2_Stream2, DMA2_Stream3, DMA2_Stream4, DMA2_Stream5, DMA2_Stream6, DMA2_Stream7
    };
    if (stream_num >= 16) {
        return 0xffffffff;
    }
    DMA_Stream_TypeDef* stream = streams[stream_num];
    bool is_reset = (stream->CR == 0x00000000)
                 && (stream->NDTR == 0x00000000)
                 && (stream->PAR == 0x00000000)
                 && (stream->M0AR == 0x00000000)
                 && (stream->M1AR == 0x00000000)
                 && (stream->FCR == 0x00000021);
    uint8_t channel = ((stream->CR & DMA_SxCR_CHSEL_Msk) >> DMA_SxCR_CHSEL_Pos);
    uint8_t priority = ((stream->CR & DMA_SxCR_PL_Msk) >> DMA_SxCR_PL_Pos);
    return (is_reset ? 0 : 0x80000000) | ((channel & 0x7) << 2) | (priority & 0x3);
}
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
extern "C" int main(void) {
    // This procedure of building a USB serial number should be identical
    // to the way the STM's built-in USB bootloader does it. This means
    // that the device will have the same serial number in normal and DFU mode.
    uint32_t uuid0 = *(uint32_t *)(UID_BASE + 0);
    uint32_t uuid1 = *(uint32_t *)(UID_BASE + 4);
    uint32_t uuid2 = *(uint32_t *)(UID_BASE + 8);
    uint32_t uuid_mixed_part = uuid0 + uuid2;
    serial_number = ((uint64_t)uuid_mixed_part << 16) | (uint64_t)(uuid1 >> 16);

    uint64_t val = serial_number;
    for (size_t i = 0; i < 12; ++i) {
        serial_number_str[i] = "0123456789ABCDEF"[(val >> (48-4)) & 0xf];
        val <<= 4;
    }
    serial_number_str[12] = 0;

    // Init low level system functions (clocks, flash interface)
    system_init();

    /**
     * 从 NVM (芯片 Flash) 中加载 (读取) 电机配置参数。由于闪存接口在 board_init() 初始化，
     * 所以要求读取配置要在 system_init() 函数之后调用。
     */

    // Load configuration from NVM. This needs to happen after system_init()
    // since the flash interface must be initialized and before board_init()
    // since board initialization can depend on the config.
    size_t config_size = 0;
    bool success = config_manager.start_load()
            && config_read_all()
            && config_manager.finish_load(&config_size)
            && config_apply_all();/*读取后将设置应用到驱动*/
    if (success) {
        odrv.user_config_loaded_ = config_size;
    } else {
        config_clear_all();
        config_apply_all(); /*将默认的参数应用到驱动*/
    }

    // Init board-specific peripherals
    if (!board_init()) {
        for (;;); // TODO: handle properly
    }

    // Init usb irq binary semaphore, and start with no tokens by removing the starting one.
    osSemaphoreDef(sem_usb_irq);
    sem_usb_irq = osSemaphoreCreate(osSemaphore(sem_usb_irq), 1);
    osSemaphoreWait(sem_usb_irq, 0);

    // Create an event queue for UART
    osMessageQDef(uart_event_queue, 4, uint32_t);
    uart_event_queue = osMessageCreate(osMessageQ(uart_event_queue), NULL);

    // Create an event queue for USB
    osMessageQDef(usb_event_queue, 7, uint32_t);
    usb_event_queue = osMessageCreate(osMessageQ(usb_event_queue), NULL);

    osSemaphoreDef(sem_can);
    sem_can = osSemaphoreCreate(osSemaphore(sem_can), 1);
    osSemaphoreWait(sem_can, 0);

    // Create main thread
    osThreadDef(defaultTask, rtos_main, osPriorityNormal, 0, stack_size_default_task / sizeof(StackType_t));
    defaultTaskHandle = osThreadCreate(osThread(defaultTask), NULL);

    // Start scheduler
    osKernelStart();
    
    for (;;);
}

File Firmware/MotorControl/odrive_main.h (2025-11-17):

#ifndef __ODRIVE_MAIN_H
#define __ODRIVE_MAIN_H

// Hardware configuration
#include <board.h>

#ifdef __cplusplus
#include <task_timer.hpp>
extern "C" {
#endif

// OS includes
#include <cmsis_os.h>

// extern const float elec_rad_per_enc;
extern uint32_t _reboot_cookie;

extern uint64_t serial_number;
extern char serial_number_str[13];

#ifdef __cplusplus
}

typedef struct {
    bool fully_booted;
    uint32_t uptime; // [ms]
    uint32_t min_heap_space; // FreeRTOS heap [Bytes]
    uint32_t max_stack_usage_axis; // minimum remaining space since startup [Bytes]
    uint32_t max_stack_usage_usb;
    uint32_t max_stack_usage_uart;
    uint32_t max_stack_usage_startup;
    uint32_t max_stack_usage_can;
    uint32_t max_stack_usage_analog;

    uint32_t stack_size_axis;
    uint32_t stack_size_usb;
    uint32_t stack_size_uart;
    uint32_t stack_size_startup;
    uint32_t stack_size_can;
    uint32_t stack_size_analog;

    int32_t prio_axis;
    int32_t prio_usb;
    int32_t prio_uart;
    int32_t prio_startup;
    int32_t prio_can;
    int32_t prio_analog;
} SystemStats_t;

struct PWMMapping_t {
    float min = 0;
    float max = 0;
};

// @brief general user configurable board configuration
struct BoardConfig_t {
    float max_regen_current = 0.0f;
    float brake_resistance = DEFAULT_BRAKE_RESISTANCE; /*如果没有使能刹车电阻，刹车电阻设置值不生效，刹车电阻为任何值都可以*/
    bool enable_brake_resistor = false; /*如果没有使能刹车电阻，刹车电阻设置值不生效，刹车电阻为任何值都可以*/
    float dc_bus_undervoltage_trip_level = DEFAULT_MIN_DC_VOLTAGE;      //<! [V] minimum voltage below which the motor stops operating
    float dc_bus_overvoltage_trip_level = 1.07f * HW_VERSION_VOLTAGE;   //<! [V] maximum voltage above which the motor stops operating.
                                                                        //<! This protects against cases in which the power supply fails to dissipate
                                                                        //<! the brake power if the brake resistor is disabled.
                                                                        //<! The default is 26V for the 24V board version and 52V for the 48V board version.

    /**
     * If enabled, if the measured DC voltage exceeds `dc_bus_overvoltage_ramp_start`,
     * the ODrive will sink more power than usual into the the brake resistor
     * in an attempt to bring the voltage down again.
     * 
     * The brake duty cycle is increased by the following amount:
     *  vbus_voltage == dc_bus_overvoltage_ramp_start  =>  brake_duty_cycle += 0%
     *  vbus_voltage == dc_bus_overvoltage_ramp_end  =>  brake_duty_cycle += 100%
     * 
     * Remarks:
     *  - This feature is active even when all motors are disarmed.
     *  - This feature is disabled if `brake_resistance` is non-positive.
     */
    bool enable_dc_bus_overvoltage_ramp = false;
    float dc_bus_overvoltage_ramp_start = 1.07f * HW_VERSION_VOLTAGE; //!< See `enable_dc_bus_overvoltage_ramp`.
                                                                      //!< Do not set this lower than your usual vbus_voltage,
                                                                      //!< unless you like fried brake resistors.
    float dc_bus_overvoltage_ramp_end = 1.07f * HW_VERSION_VOLTAGE; //!< See `enable_dc_bus_overvoltage_ramp`.
                                                                    //!< Must be larger than `dc_bus_overvoltage_ramp_start`,
                                                                    //!< otherwise the ramp feature is disabled.

    float dc_max_positive_current = INFINITY; // Max current [A] the power supply can source
    float dc_max_negative_current = -0.01f; // 电源可以吸收的反电动势电流，Max current [A] the power supply can sink. 
                                            // You most likely want a non-positive value here. Set to -INFINITY to disable.
    PWMMapping_t pwm_mappings[4];
    PWMMapping_t analog_mappings[17];
};

struct TaskTimes {
    TaskTimer sampling;
    TaskTimer control_loop_misc;
    TaskTimer control_loop_checks;
    TaskTimer dc_calib_wait;
};


// Forward Declarations
class Axis;
class Motor;

#include "autogen/interfaces.hpp"

// ODrive specific includes
#include <utils.hpp>
#include <low_level.h>
#include <encoder.hpp>
#include <sensorless_estimator.hpp>
#include <controller.hpp>
#include <current_limiter.hpp>
#include <thermistor.hpp>
#include <trapTraj.hpp>
#include <endstop.hpp>
#include <mechanical_brake.hpp>
#include <axis.hpp>
#include <oscilloscope.hpp>
#include <communication/communication.h>
#include <communication/can/odrive_can.hpp>

// Defined in autogen/version.c based on git-derived version numbers
extern "C" {
extern const unsigned char fw_version_major_;
extern const unsigned char fw_version_minor_;
extern const unsigned char fw_version_revision_;
extern const unsigned char fw_version_unreleased_;
}
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

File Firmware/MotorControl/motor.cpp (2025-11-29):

#include "motor.hpp"
#include "axis.hpp"
#include "low_level.h"
#include "odrive_main.h"

#include <algorithm>

static constexpr auto CURRENT_ADC_LOWER_BOUND = (uint32_t)((float)(1 << 12) * CURRENT_SENSE_MIN_VOLT / 3.3f);
static constexpr auto CURRENT_ADC_UPPER_BOUND = (uint32_t)((float)(1 << 12) * CURRENT_SENSE_MAX_VOLT / 3.3f);

/**
 * @brief This control law adjusts the output voltage such that a predefined
 * current is tracked. A hardcoded integrator gain is used for this.
 * 
 * TODO: this might as well be implemented using the FieldOrientedController.
 */
struct ResistanceMeasurementControlLaw : AlphaBetaFrameController {
    void reset() final {
        test_voltage_ = 0.0f;
        test_mod_ = std::nullopt;
    }

    ODriveIntf::MotorIntf::Error on_measurement(
            std::optional<float> vbus_voltage,
            std::optional<float2D> Ialpha_beta,
            uint32_t input_timestamp) final {

        if (Ialpha_beta.has_value()) {
            actual_current_ = Ialpha_beta->first;
            test_voltage_ += (kI * current_meas_period) * (target_current_ - actual_current_);
            I_beta_ += (kIBetaFilt * current_meas_period) * (Ialpha_beta->second - I_beta_);
        } else {
            actual_current_ = 0.0f;
            test_voltage_ = 0.0f;
        }
    
        if (std::abs(test_voltage_) > max_voltage_) {
            test_voltage_ = NAN;
            return Motor::ERROR_PHASE_RESISTANCE_OUT_OF_RANGE;
        } else if (!vbus_voltage.has_value()) {
            return Motor::ERROR_UNKNOWN_VBUS_VOLTAGE;
        } else {
            float vfactor = 1.0f / ((2.0f / 3.0f) * *vbus_voltage);
            test_mod_ = test_voltage_ * vfactor;
            return Motor::ERROR_NONE;
        }
    }

    ODriveIntf::MotorIntf::Error get_alpha_beta_output(
            uint32_t output_timestamp,
            std::optional<float2D>* mod_alpha_beta,
            std::optional<float>* ibus) final {
        if (!test_mod_.has_value()) {
            return Motor::ERROR_CONTROLLER_INITIALIZING;
        } else {
            *mod_alpha_beta = {*test_mod_, 0.0f};
            *ibus = *test_mod_ * actual_current_;
            return Motor::ERROR_NONE;
        }
    }

    float get_resistance() {
        /*根据相电压和采样到的相电流，根据欧姆定律计算出电机相电阻*/
        return test_voltage_ / target_current_;
    }

    float get_Ibeta() {
        return I_beta_;
    }

    const float kI = 1.0f; // [(V/s)/A]
    const float kIBetaFilt = 80.0f;
    float max_voltage_ = 0.0f;
    float actual_current_ = 0.0f;
    float target_current_ = 0.0f;
    float test_voltage_ = 0.0f;
    float I_beta_ = 0.0f; // [A] low pass filtered Ibeta response
    std::optional<float> test_mod_ = NAN;
};
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

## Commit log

2025-11-16 硬件电路测试，添加数据手册，原理图，更新驱动器和 AS5047P 硬件设计
    [AS5047P.kicad_pcb, AS5047P.kicad_sch, AS5047P_BOM.dxf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]
2025-11-17 添加Firmware文件
2025-11-17 移除测试程序，STM32中断函数统一放置到stm32f4xx_it文件，GPIO不命名
2025-11-17 移除Stm32SpiArbiter结构config配置定制字段，SPI统一配置(经过2x验证电机工作正常)
2025-11-17 中断处理使用HAL_GPIO_EXTI_IRQHandler，方便驱动替换((经过2x验证电机工作正常))
2025-11-17 PWM控制信号驱动修改通道GPIO指定方式（经过2x验证工作正常）
2025-11-17 Stm32SpiArbiter发送任务队列和Motor刹车配置逻辑整理（经过2x验证工作正常）
2025-11-17 移除多余函数接口，添加定时器寄存器配置说明，整理程序（经过2x验证工作正常）
2025-11-17 使用LetterShell替换LibFibre+Python实现命令控制，可不依赖Python脚本独立运行（经过2x验证工作正常）
2025-11-17 增加固件说明，解决USBD_CDC_DataOut调用Receive接口时没有向下传递hEP_Rx->Buffer导致CDC_Receive_FS获取Buf指针时为NULL导致接收数据为未知无效数据问题
2025-11-27 完成CAN接口和对应GPIO调试，增加Shell指令，增加CAN协议和控制指令，更新README文件（经过2x验证，工作正常）
2025-11-29 CAN协议增加位置速度，力位混控协议，电流/力矩反馈协议（经过2x验证，工作正常）
